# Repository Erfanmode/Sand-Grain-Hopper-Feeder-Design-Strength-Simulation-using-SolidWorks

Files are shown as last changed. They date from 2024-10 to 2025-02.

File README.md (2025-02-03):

# Sand & Grains Hopper Feeder Design & Strength Simulation using SolidWorks - Spring 2022
In this project, we design a sand and grain hopper feeder for the capacity of 30 Tons. Feeder is able to push out the sand and grains
with high moisture. Additionally, it can withstand powerful winds and high magnitude of earthquakes. Huge shout-out to my dear friend and teammate [Reyhane Nikoobayan](https://github.com/ReyhaneNikoobayan) for her contribution to this project.
{31DD2E23-A9A7-48DF-8576-A2769300EA40}
{AE516640-4FAC-4123-9A2C-66D67296858D}
## This Project Contains:
- Dynamic Force and Static Load Analysis
- Strength of Material Estimation
- Design using SolidWorks
- Finite Element Analysis
- Grain Slipping Analysis
- Welded Surface Tension Analysis
- Bolt and Screw Tension Analysis
- Steel Beam Strength Analysis

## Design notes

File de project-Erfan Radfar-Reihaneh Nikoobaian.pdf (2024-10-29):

## به نام خدا

گزارش پروژه پیچ و جوش درس طراحی اجزاء 1

اعضاء:

ریحانه نیکوبیان 99106747 عرفان رادفر 99109603

نام استاد : دکتر محمد دورعلی

خرداد 1401

فهرست

-2 فهرست

-3 صورت مسئله

-4 محاسبات اولیه

-6 به دست آوردن ضخامت ورق ها

-7 وزن اجزاء و نیروهای وارده

-7 جوش نبشی به مخزن بال

-8 جوش لچکی های پایینی

-9سطح مقطع ستون های اصلی

-10محاسبه ابعاد و تعداد پیچ های نبشی به تیر

-11 پیچ نبشی به لچکی های پایین

-12 نصب در زمین

-13 اجزاء به کار رفته

-14 تخمین قیمت

-15 منابع

-16 نقشه ها

صورت مسئله:

سیلوی مصالح دانه بندی شده

در کارخانجات صنایع معدنی موارد زیاد پیش میآید که مصالح ساختمانی مانند شن و ماسه در ابعاد مختلف باید بطور مجزا انبار شوند . این کار بدلیل آن است که بعدا در زمان استفاده مثال برای ساخت بتن یا آسفالت بتوانند با ترکیب های مختلف از این مصالح استفاده کنند . پروژه این دفعه ما در مورد طراحی برای ساخت این سیلو هاست . اگر جمله کلیدی "سیلوی ذخیره مصالح دانه بندی شده" را در مرور گر جستجو کنید و تصاویر را نگاه کنید تعداد زیادی از آنها را مشاهده میکنید . معمول این سیلو ها دارای یک بخش مکعبی در بال و یک بخش هرمی در پایین با یک حفره در پایین ترین قسمت برای تخلیه مواد هستند . حفره پایین با یک دریچه لولیی بسته شده که در موقع تخلیه باز میشود . مواد از بال به داخل آنها ریخته شده و از پایین خارج میشود . زاویه بخش هرمی را طوری می گیرند که ضمن داشتن بیشترین حجم زاویه مناسب برای سر خوردن مصالح و تخلیه را دارا باشد . این سیلو ها معمول با ورق ساخته شده و پایه های آنها از آلت ساختمانی ساخته میشود که با پیچ و مهره بهم متصل میشوند . این سیلو ها میتوانند دارای پایه های بلند باشند که کامیون مستقیما زیر آنها برود و کامیون را با آنها بارگیری کنند . کامیون دنده عقب به زیر آنها میرود و وقتی پر شد از زیر سیلوخارج میشود . 50داشته باشد و بتوانند m به کارخانه ما سفارش 4 عدد از این سیلو ها داده شده که هر یک ظرفیت 3 کامیون را بارگیری کنند . مشتری بدلیل اینکه محل استقرار این سیلو ها را تغییر میدهد عالقمند است که آنها طوری طراحی شوند که بتوان در حالت دمونتاژ شده با حد اقل ارتفاع و ابعاد آنها را روی تریلر بارگیر ی نموده و در محل با یک جرثقیل نه چندان ظرفیت بال این سیلو ها را دوباره مونتاژ کرد . این سیلو ها را طراحی، نقشه مونتاژی و نقشه های قطعات را استخراج نموده و با ذکر مالحظات ساخت مونتاژی، لیست مواد، و برآورد قیمت اجرای پروژه منجمله هزینه های مهندسی به تفکیک در قالب یک گزارش تحویل دهید .

محاسبات اولیه ابعاد:

در طراحی اعضای این سازه ، به علت عبور کامیون و راننده کامیون و کارکنان محیطی که از سیلو استفاده میشود، ضریب اطمینان را 4 میگیریم.

عرض کامیون حدود 2.4 متر است که آینه ها حدود 10 سانت از عرض کامیون بیشتر است و برای راحتی حرکت کامیون عرض مخزن را 3 متر درنظر می گیریم تا کامیون بتواند مانور داشته باشد. برای طراحی با قابلیت محاسبه راحت تر و تقارن و استفاده از ورق 1.5 *6 طول مخزن را نیز 3 متر در نظر می گیریم.ارتفاع کامیون حدود 3 متر است و ممکن است لبه ای برای بارگیری داشته باشیم و همچنین ماسه ها ک په شوند ارتفاع تیرها تا پیش از مخزن خروجی را 3.8 در نظر می گیریم که با محاسبه ارتفاع قیف و دریچه و طول پیچ شده تیر به مخزن تیر باید به ارتفاع باشد

زاویه ریزش ماسه خیس با توجه به اینکه زاویه اصطکاک ماسه و فولد 22 درجه است در نمودار Jenicke (https://powderprocess.net/Silo_discharge.html) و با توجه به زاویه اصطکاک داخلی 45 درجه است زاویه ریزش ماسه خیس 60 درجه به دست می آید.

3-0.4=2.6

2.6*0.5=1.3

h1= 1.3*tan(60)=2.2517

3 =7.769 m ⁰.4∗0.4∗0.346
3

3∗3∗2.596
3

V hopper=

=4.69 m

50−7.769
3∗3

H tank=

همچنین برای دریچه خروجی ارتفاع را 40 سانتی متر تخمین می زنیم و

با توجه به اینکه پین باید وزن ماسه را تحمل کند و ماسه را سیال در نظر می گیریم پس قطر پین را با در نظر گرفتن تحمل تنش برشی به دست می آوریم.

Ƭy
4

=

(2000∗(4.69+2.25+0.4)∗9.8∗0.4^2) 2∗r

2∗π
Fs=4

r=8.9

Ty=Q/2=370/2=185 MPa

اما ما بر اساس دید مهندسی قطر را 4سانتی متر در نظر می گیریم و برای زدن جوش و جلوگیری از تمرکز تنش 1.5 برابر قطر از لبه بالیی فاصله می گذاریم و فاصله مرکز پین تا لبه بالیی 8 سانتی متر می شود و ارتفاع مثلث قِام الزاویه ما 22 سانتی متر و طول قاعده اش 40 سانتی متر است بنابراین
0.48=0.3*0.4*0.4 می | 3m | زاویه دریچه ما به 84.5 میرسد.همچنین حجم مخزن خروجی ما به
رسد.

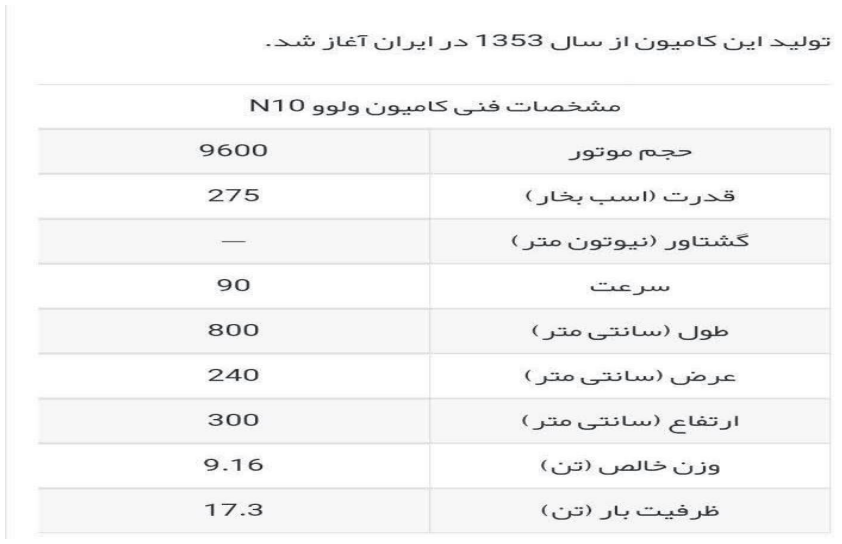
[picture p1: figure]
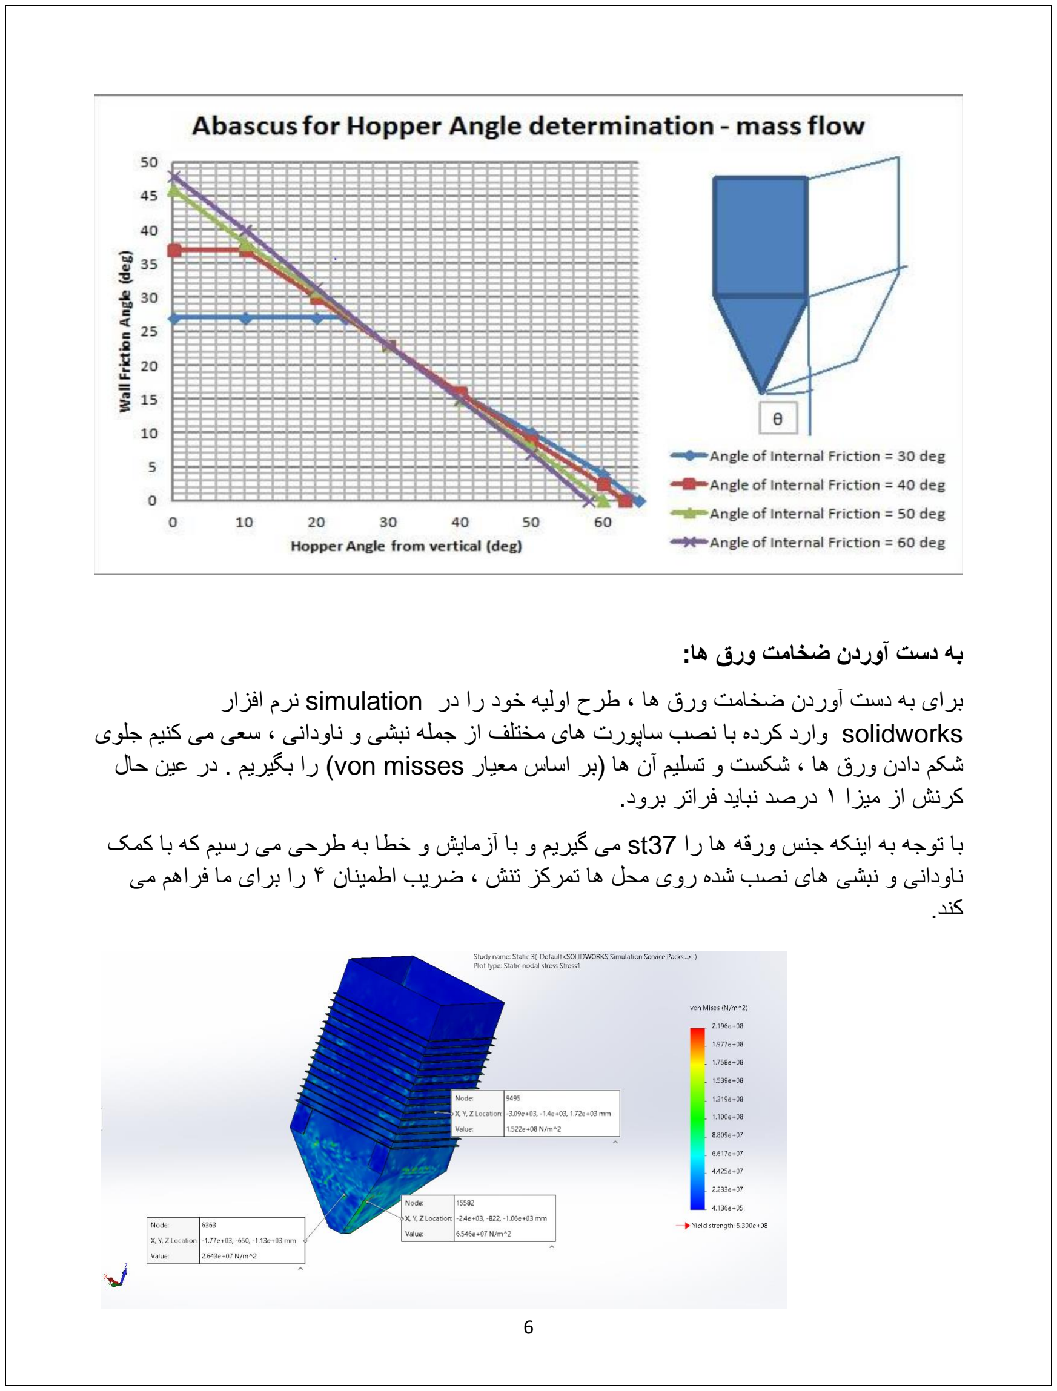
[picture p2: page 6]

به دست آوردن ضخامت ورق ها:

برای به دست آوردن ضخامت ورق ها ، طرح اولیه خود را در simulation نرم افزار solidworks وارد کرده با نصب ساپورت های مختلف از جمله نبشی و ناودانی ، سعی می کنی م جلوی شکم دادن ورق ها ، شکست و تسلیم آن ها ) بر اساس معیار misses von )را بگیریم . در عین حال کرنش از میزا 1 درصد نباید فراتر برود.

با توجه به اینکه جنس ورقه ها را 37st می گیریم و با آزمایش و خطا به طرحی می رسیم که با کمک ناودانی و نبشی ها ی نصب شده روی محل ها تمرکز ت نش ، ضریب اطمینا ن 4 را برای ما فراهم می کند.

در این شبیه سازی محل تکیه گاه، محا نصب ستون ها در نظر گرفته شده تا شرایط سازه اصلی از نظر اعمال نیرو و تنش مهیا باشد.

KN 44.43=9.81 *8030*12*0.01*4.7 وزن مخزن بال )جداره(

m/kg 8030 | 3 | چگالی فولد

KN 13.93=9.81*8030*0.01)*2.6*1.7*(4 وزن قیف )جداره(

(3∗3∗2.6∗sin(60)−0.4

2
∗0.346)
3

*9.81*2000 وزن قیف )ماسه(

KN 830.0=9.81*2000 *4.7 *3*3 وزن مخزن بال )ماسه(

KN 0.942=0.4*0.4*0.3*2000*9.81 وزن دریچه پایین )ماسه(

KN 0.472=8030*9.81*0.01*5*0.3*0.4 وزن دریچه پایین )جداره(

وزنی که لچکیهای پایینی تحمل می کند = وزن جداره قیف + وزن ماسه قیف + وزن ماسه مخزن

13.93+132.2+830+0.942+0.472=977.5 KN

وزنی که نبشی های متصل بهمخزن بالیی تحمل می کنند=وزن جداره قیف و مخزن + وز ن ماسه قیف و مخزن

13.93+132.2+830+44.43+0.942+0.472=1022 KN

برای وزن ناودانی و نبشی و لچک حدود 20 کیلونیوتون به این اعداد اضافه می شود

8 ناودونی مخزن +حدود 2 ناودونی برای قیف +نبشی بین قیف و مخزن و نبشی های مخزن و قیف16+ لچکی

وزن نبشی ها KN 14=9.81*8030*

-6 42*4500*10

وزن ناودانی ها KN 3.3=9.81*34*10

وزن لچکی ها حدود 2 کیلو نیوتون می گیریم و مجموع وزن اتصالت به 20 کیلونیوتون می رسد

جوش نبشی به مخزن باال:

نیرویی که به جوش نبشی متصل کننده ستون ها و بدنه وارد میشود حاصل از نیروی باد ) با استفاد ه از جداول استاند ا (https://eurocodeapplied.com/design/en1991/wind-force-rectangular)رد (https://eurocodeapplied.com/design/en1991/wind-force-rectangular) برای سطح مقطع مستطیلی بدست میآید.( و همین طور نیروی حاصل از اصطکاک

ماسه های داخل مخزن که نسبت کمی از وزن )در حدود 10 درصد ( را دارد. اما با توجه به اینکه سازه ما باید در مواقع زلزله هم با بار پر ، بتواند پایستار باقی بماند می بایست بتواند حداکثر شتاب افقی زلزله (https://en.m.wikipedia.org/wiki/Peak_ground_acceleration) را تحمل کند .

این مقدار برای زلزله هایی با شدت ت خریب 9 )زلزله ای مانند زلزله بم( کمتر از شتاب جاذبه زمین می-باشد. برای همین در محاسبات ، نیرویی افقی برابر وزن مخزن و ماسه به سازه وارد میشود.

در هنگا م زلزله ، جوش نبشی در دو تیر با نیرو ی حداکثر، نیروی 890 کیل ونیوتن را تحمل میکند. از طرفی چون نیروی تیر با فاصله تقریبا نصف عرض نبشی به آن وارد می شود، خمش نیز برای خط جوش بال و پایی ن آن رخ میدهد.)تنش خمش حدود نصف تنش برش می باشد.(

در نتیجه با توجه به معاد له زیر ، حداکثر تنش بر شی در کمترین سطح جوش بدست میآید.

Tmax=

F
0.707.ℎ.l

+

F∗

d
2

∗

d
2
0.707.ℎ.b.

d2
2

= 1.5

F
0.707.ℎ.l

=

94∗ 10⁶

4

Fs=4

∑M=0 47*4.7+1042*2.35=3*F2

Min(0.4Sy;0.3Su)=94

Sy=235 Mpa ; Su=370 Mpa

3∗(44+100+4∗f)∗10³

2∗(0.707∗16∗ℎ)

=

94
4

∗ 10⁶
f=445KN | h=10.9 mm

چون ضخامت 10 میلی متر است جوش 7 میلی متر می زنیم.) از 0.7 ضخامت ورق ، ارتفاع جوش بیشتر نمیشود.(

ضریب اطمینان و طراحی کاهش مییابد اما چون زلزه در مدت کوتاه و احتمال کمی رخ می دهد ، این کاهش ضریب اطمینان قابل قبول است.

جوش لچکی های پایین ی :

لچکی ها می باید نیروی وزن قیف و شنوماسه بالی آن را تحمل کند . پا فرض ارتفاع جوش mm7 به طول جوش زیر میرسیم.

977.5∗10³

0.707∗0.007∗l

=

94∗10⁶

4∗2

L=16.808 m

چون طول جوش خورده لچکی ها از دو طرف cm30 می باشد )15 سانت از سطح لچکی از د و وجه به نبشی و بدنه قیف تماس دارد. ( پس به 14 لچکی از هر طرف نیاز داریم.

هر طرف 14 لچکی 56=16.808/0.3=N

با توجه به ضخامت لچکی ها ) ضخامت هر لچکی 10 میلی متر از ورق مورد استفاده د ر بدنه( نگرانی نسبت به شکست و تسلیم آن ها نداریم.

سطح مقطع ستون های اصلی:

چهار ستون اصلی تحت نیروی عمودی ، در معرض کمانش قرار خواه ند گرفت. با توجه به شکل کمانش آن ها ) یک سر درگیر و یک سر آزاد ( از معادله زیر استفاده میکنیم.

Pcr=

π

2
.E .I
L

2

Le=2L L=3.8+0.4+2.44=6.64m E =206 Gpa

Pcr=445+261=706 KN

Imin=22.6*10⁻⁵ m⁴

2 | اندازه Imin برابر با

cm22600 به دست میآید که همچین تیری در جدول تیرهای استاندارد نداریم.
اما می توانیم تیری با Imax فوق به دست آورده و در راستای عمود محور ممان ضعیف آن ، تیرهای ضربدری را قرار ده یم که باعث میشود طول موثر تیرها در راستای کمانش کاه ش یابد و تیر تقو یت شود.

Iy=22930 cm⁴

Iz=6990 cm⁴

) | جدول | از | انتخابی | )Imin=7890 | HE-A PBI 320

با توجه به مطالب بال تیر 320 PBA A-HE را از جدول انتخاب می کن یم.

جوش تیر به فلنج باالیی:

برای اتصال تیرها به بد نه از پیچ استفاده می کنیم تا قابلیت دمونتاژ شدن داشته باشد. برای اینکه تیره ای به صورت عمودی زیر نبشی مخزن بالیی نصب شوند ) برای کا هش ارتفاع موثر(، بایند فلنجی به سر بالیی آن ج وش دهیم تا و سپس سوراخ پیچ ها را بر روی آن و نبشی ایجاد کنیم.

این جوش باید بتواند نیروی برشی باد و زلزله را تحمل کند.

Tmax=

F
0.707.ℎ.l
N 1089(=نیروی باد(+47(نیروی زلزله)1042=F 94 ∗ 10⁶
4

=

1089 ∗ 10³
4 ∗ 0.707 ∗ ℎ ∗ 1.8

h=9.1 mm

اما ما جوش تیر را 7 میلی متر می زنیم که کمی ضریب اطمینان را تنها در برابر زلزله پایین می اورد که البته به خاطر احتمال کم زلزله و مدت کوتاه آن، این ضریب قا بل قبول است. )3.07=Fs )

محاسبه ابعاد و تعداد پیچ های نبشی به تیر:

اولین گزینه : پیچ 6.8

τ max=√τ
2 +

σ²
4
σ = x ∗ Sp

Sp=0.85 Sy

موقع زلزله

Sp
4

2
>(

X.Sp
2

−

706
N.At

)

2+(Fs.706
N.Ar

)

2

Sp=0.85(600*0.8)=408 MPa

Fs=4 Ar=52.3 mm²

x=0.9 At=58 mm²

ترم اول در محاسبات کوچکتر از صفر می شود پس نیروی عمود بر سطح پیچ ها وارد نمیکند و آن را صفر می گذاریم.

204 > ( ⁴∗272
N∗52.3

تعداد پیچ 101=N)

زلزله نباشد

204>√183.6
2 +

47
N.Ar.10³

تعداد پیچ 10=N

290/25=11

در نتیجه ب ه حدود 100 پیچ برای هر ستون نیاز داریم اما تعداد پیچ ز یاد به قیمت افزایش ابعاد فلنج جوش شده به تیر تم ام میشود پس 60 پیچ قرار می دهیم که ضریب اطمینان را تا 2.4 پایین میآورد.

اما به علت احتمال کم زلزله و نیروی کوتاه مدت آن ، این اندازه قابل قب ول است.

د ر انتها باید دقت شود که در سر تیرها به خاطر اعمال نیرو در سطح کم، احتمال خم شد ن و پیچش نبشی بالیی وجود د ارد، پس در آن نقاط برای هر سطون 5، لچکی در داخل نبشی به دو طرف جوش میدهیم تا مانند خرپ ا عمل کند. لچک ی ها ضخامت 10 و مثلث های قائ م الزا ویه به ابعاد 150* 150 می باشد که 20 میلی متر از راس آن ها بریده شده است. جوش ماهیچه ی آن ها سرتاسری و به ارتفاع 7 میلی متر خواهد بود.

پیچ نبشی به لچکی های پایین

برای اتصال لچکی هایی که قیف پایی ن را نگه داشت ه اند ، از یک فلنج با طول بلند استفاده می شود )1650 میلی متر تا با ستو ن ها تالقی پیدا نکنند (. سپس نبشی مخزن بالیی و فلنج به هم پیچ می-شوند. محاسبه نیروی پیچ آن ها مانند محاسبه نیروی جوش آن هاست، با این تف اوت که به علت وج ود اهرم کوچک لچکی، خمش نیز اتفاق می افتد و تا دو برابر نیرو را با ل می برد.

در عین حال نکته مهم در این قسمت این است که فسردگی فلنج و نبشی نباید صفر شود و همیشه باید نیروی عمود ی اعضای بین پیچ و مهره منفی )فشردگی( بماند.

پس

X∗At∗Sp
FS >

(1−C) ∗ F
N∗4

که c در آن نسبت kb به مجموع kb و km می باشد. با توجه به اینکه برای دو ورق هم ضخامت و با ضخامت نزدیک به قطر پیچ ، c بین 2 و 2.5 می باشد و اینکه F محاسبه شده و At با توجه به پیچ 10 با گر ید 6.8 به دست م ی آید

F=977.5 N

) این نیرو همان نیرو قیف و ماسه بالی آن است (

اندازه N به دست می آید. این اندازه برای هر وجه مخزن است که برابر 44 پیچ می باشد. این پیچ ها در دو ردیف و به تعدا 22 در هر ردیف روی نبشی تعبیه خواهد شد.

نصب در زمین:

با توجه به اینکه وزن مخزن و قیف ر وی همدیگر 6 تن می باشد، نصب آن با جرثقیل های معمول ممکن است.

برای نصب به پایین هر کدام از مخزن هاbolt anchor وصل می شود که با توجه به این که این پیچ در خاک و بتن پایه فرو می رود ، محاسبات آن مرب وط به رشته عمران خواهد بود. در عین حال بهتر است که این مخزن در محل وزش باد شدید و خاک سست نصب نشود.

اجزاء به کار رفته:

ورق ها )همگی از جنس 37st و ضخامت 10 میلی متر(

| تعداد شکل )mm )
1500 *3000 | 12
3000*200 | 4
ارتفاع 1300 | 4 ذوزنقه ای)در نقشه قاعده ها مشخص شده(
ارتفاع 1500 | 4 ذوزنقه ای)در نقشه قاعده ها مشخص شده(
400*400 | 2
دایره | 2 400*400 با یکی از اضالع قسمتی از

پروفیل ها

| | نام قطعه طول ) mm )تعداد
4 | 6800 | HE-A PBA 320
| | ناودانی 200 2750 32
| | نبشی 150 3000 4
4 | 2500 | نبشی 150 )زاویه میان )102.45
| | نبشی 150 3800 4
| | نبشی 150 4500 4

پیج و مهره ها

576 پیچ و مهره 10 میلی متر – گرید 6.8

جوش ها )6013E )

| نوع ضخامت)mm (طول خط جوش(mm (محل جوش
به یکدیگر)افقی ( | مغزی - 12*3000 ورق های مخزن بالیی
| مغزی - 4*0.4 مکعب دریچه
یکدیگر | مغزی - (1607+1793)*4 ورق های قیف ها به
به یکدیگر) عمودی ( | ماهیچه ای 5 4*4700 ورق های مخزن بالیی
| ماهیچه ای 7 3000*8 نبشی به مخزن
| ماهیچه ای 5 4000*32 ناود ان ی ها به مخزن
| ماهیچه ای 7 300*56 لچکی ها به قیف
| ماهیچ ه ای 7 300*20 لچکی بین نبشی

تخمین قیمت:

| جنس قیمت ) هزار تومان(
| نبشی ها) 22 هزارتومان هر 12 متر( 120
| ناودانی)20 هزارتومان هر 12 م تر( 146
| پیچ و مهر ه)250 تومان پیچ و مهره( 144
| تیراهن 320 )هر 12 متر 65 هزار ت ومان( 260
| ورق 10 ، 1500* 6000 = 21.4 هزارتومان 214
6479 | الکترود 6013E ( 2.5 کیلو=167هزارتومان( 97 کیلو برای پروژه
| هزینه برق و تجهیزات جوش 2500
| هزین ه برش ومته 3000
| هزینه حمل و نقل 2800

هزینه کل: 15.6میلیون تومان

منابع:

Calculation method to Design Hoppers and Silos - Hopper and Silo Flow of powder - Flowability issues solving - Discharge throughput (Beverloo equation) (https://powderprocess.net/Silo_discharge.html)

/https://ahanonline.com

https://blog.swantonweld.com/the-various-types-of-structural-steel-shapes (https://blog.swantonweld.com/the-various-types-of-structural-steel-shapes)

https://en.m.wikipedia.org/wiki/Peak_ground_acceleration#:~:text=Pe ak%20Ground%20Acceleration%20(PGA)%20is,site%20during%20a% .20particular%20earthquake (https://en.m.wikipedia.org/wiki/Peak_ground_acceleration)

https://kimyas.ir/%D9%82%DB%8C%D9%85%D8%AA-%D9%BE%DB%8C%DA%86-%D9%88-/%D9%85%D9%87%D8%B1%D9%87 (https://kimyas.ir/%D9%82%DB%8C%D9%85%D8%AA-%D9%BE%DB%8C%DA%86-%D9%88-%D9%85%D9%87%D8%B1%D9%87/)

https://www.geotechdata.info/parameter/angle-of-friction

https://eurocodeapplied.com/design/en1991/wind-force-rectangular#:~:text=The%20basic%20wind%20velocity%20is,provided .%20in%20the%20National%20Annex (https://eurocodeapplied.com/design/en1991/wind-force-rectangular)

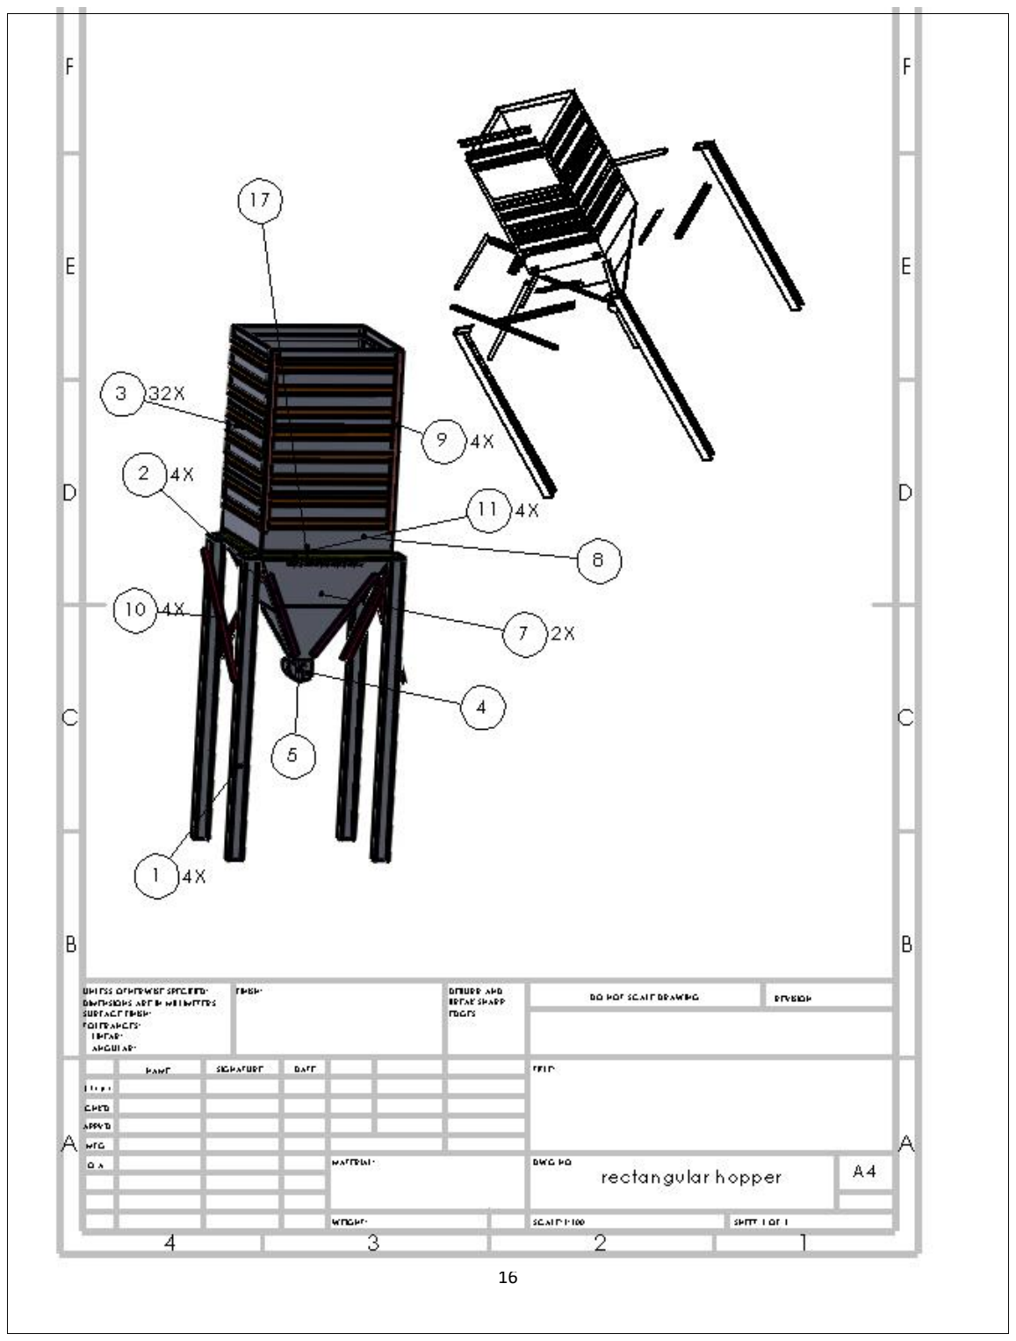
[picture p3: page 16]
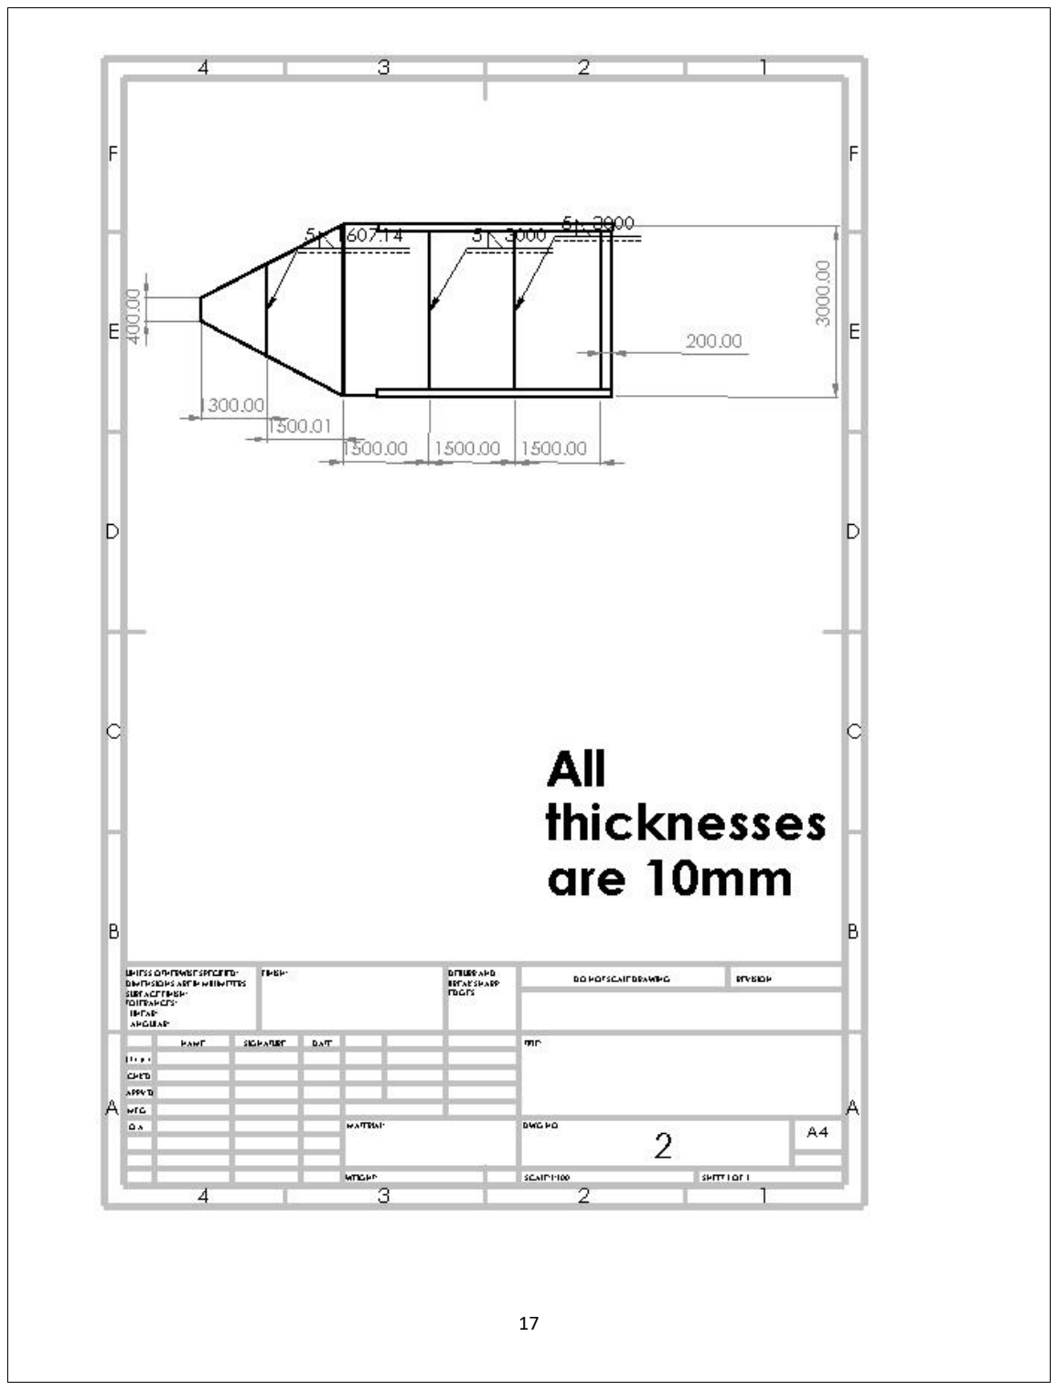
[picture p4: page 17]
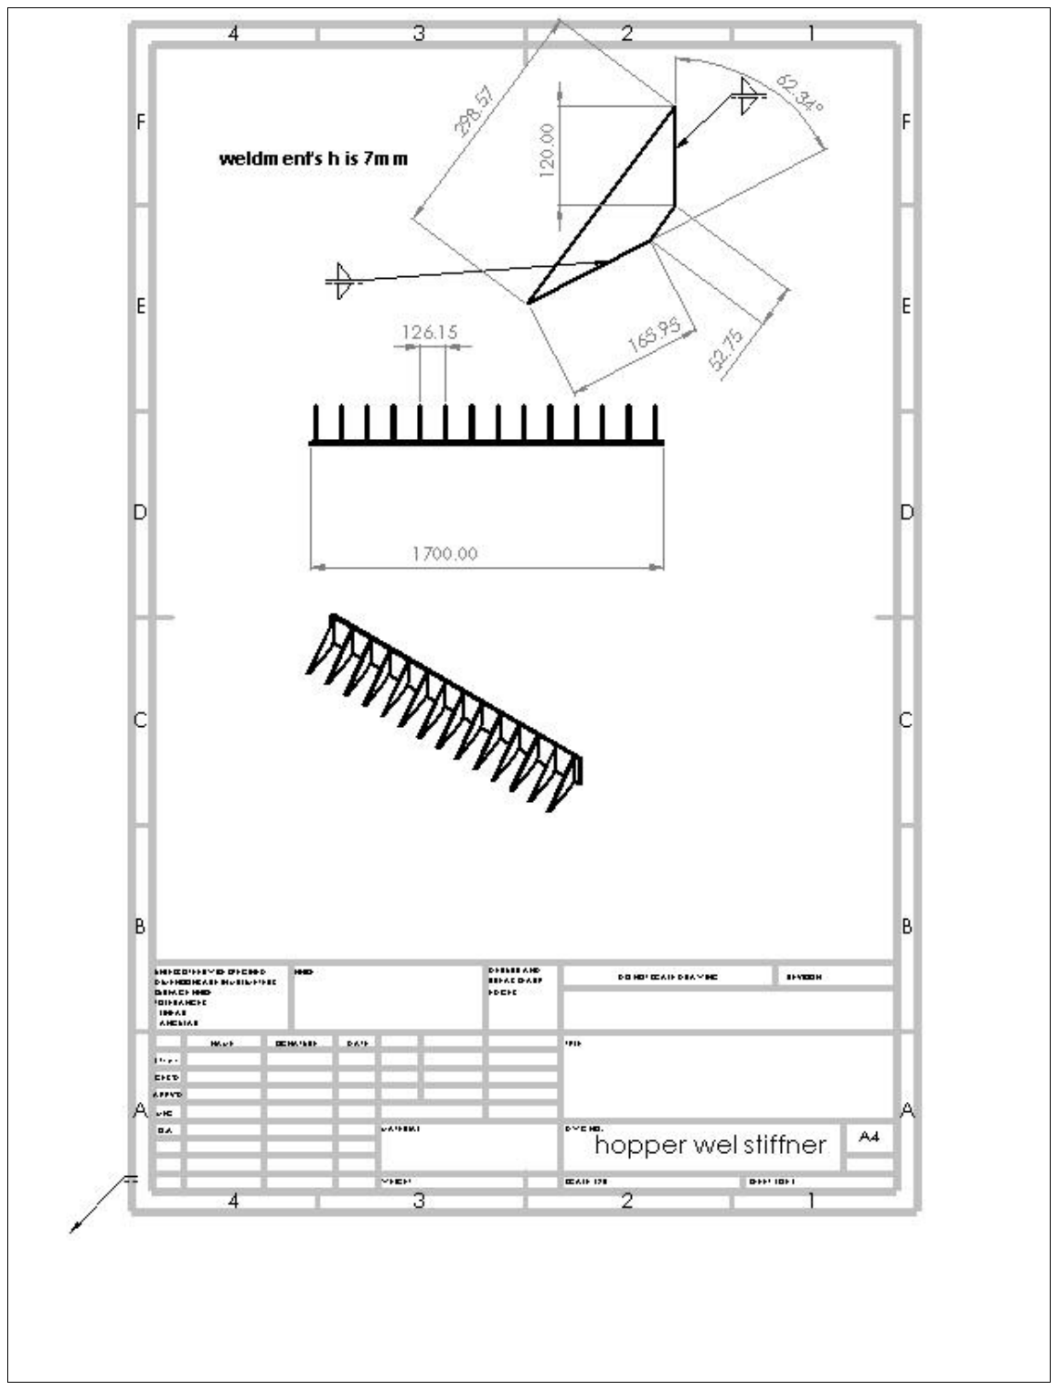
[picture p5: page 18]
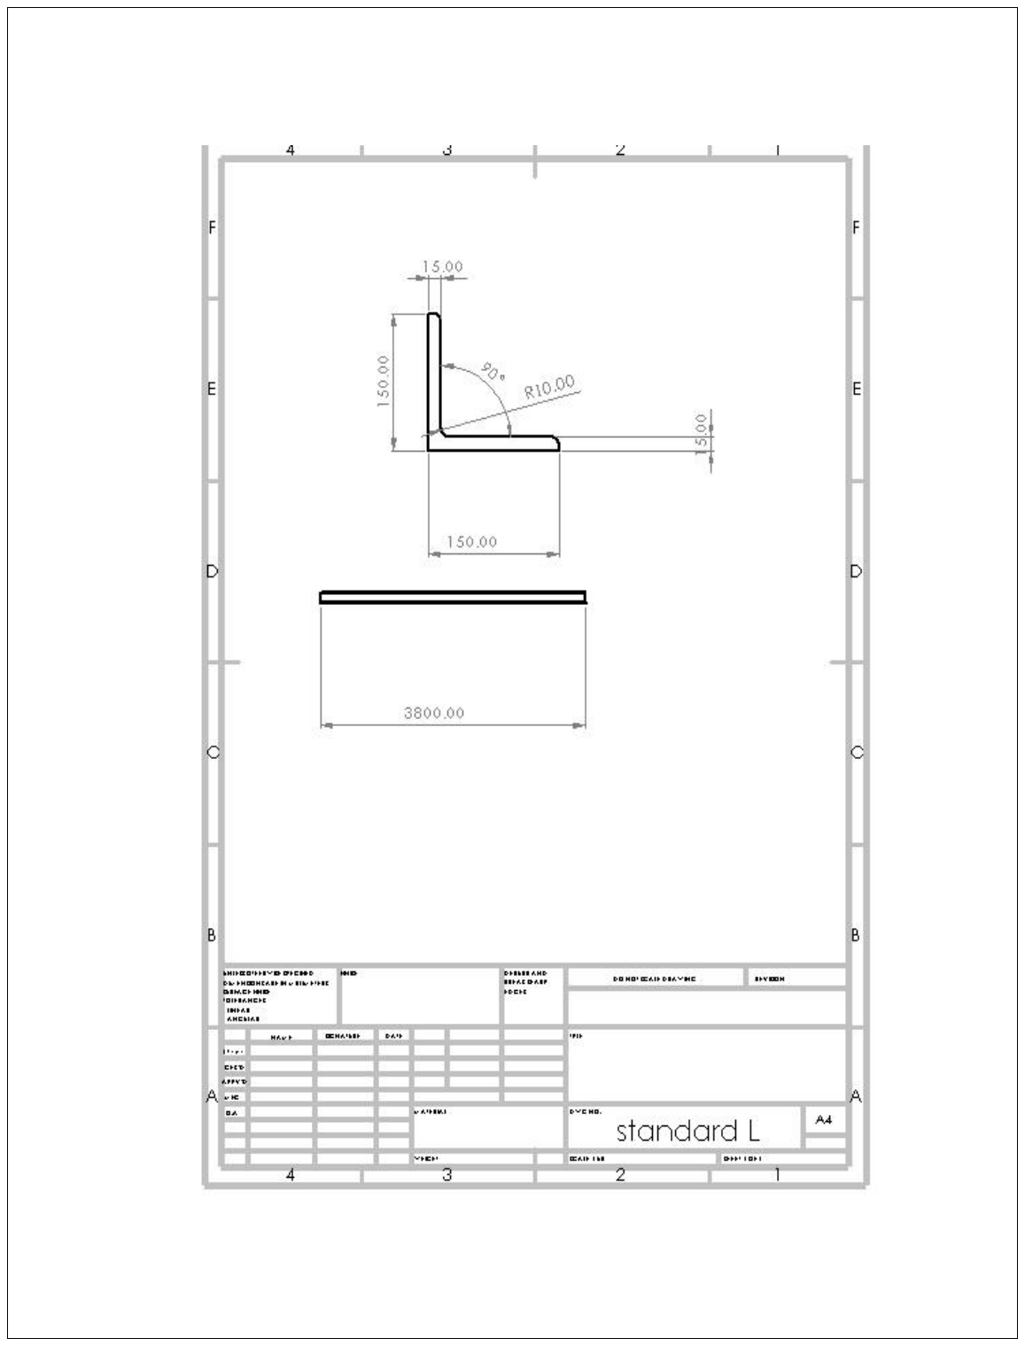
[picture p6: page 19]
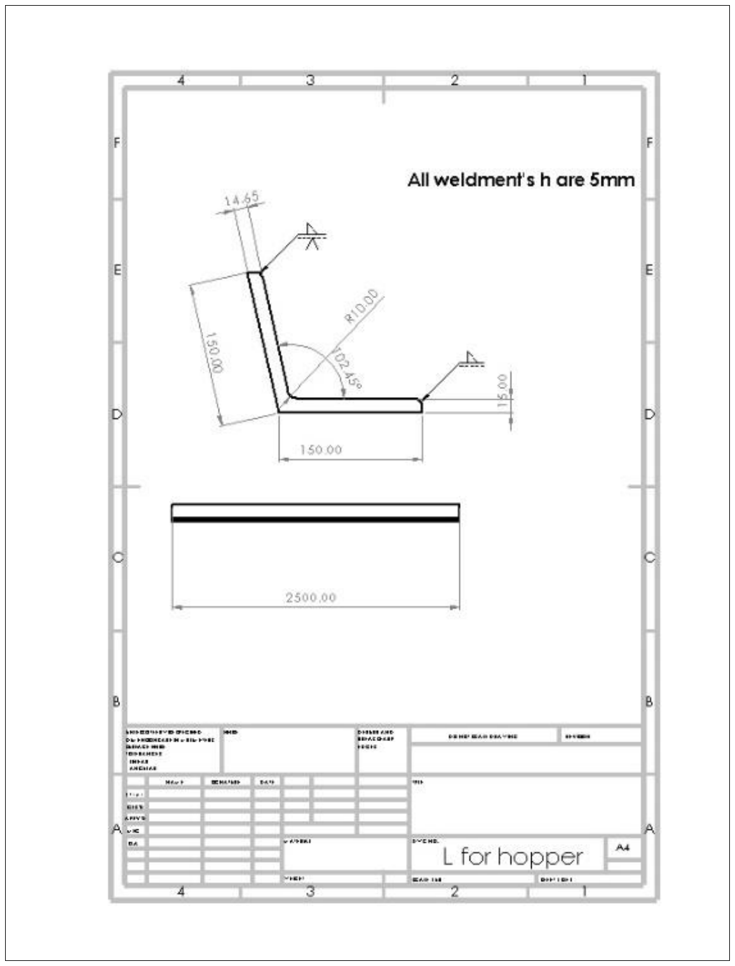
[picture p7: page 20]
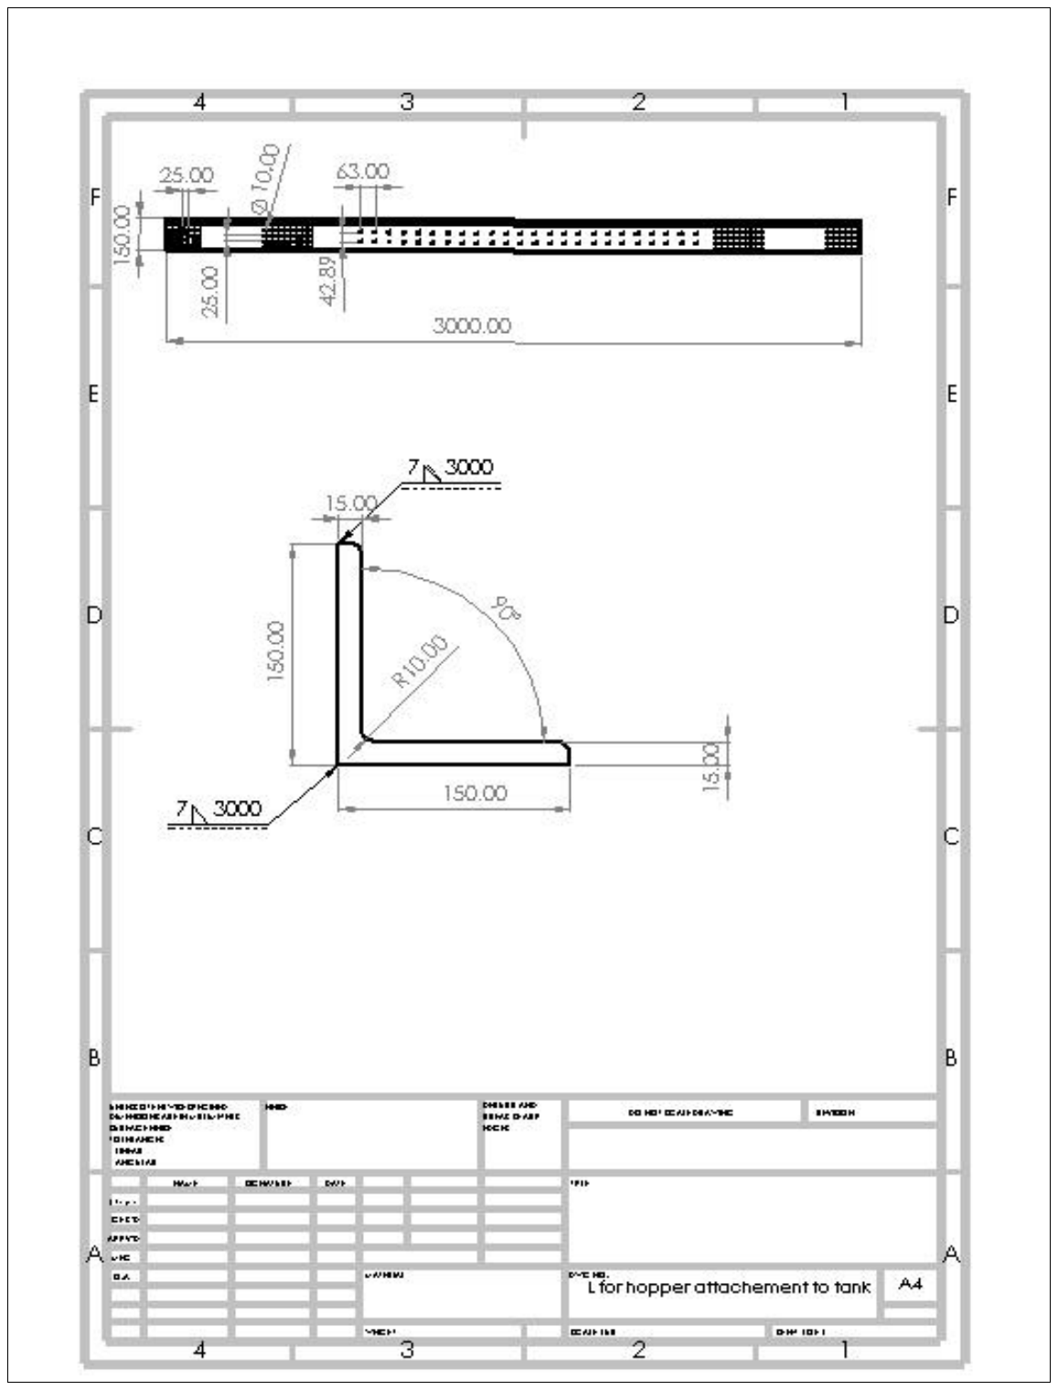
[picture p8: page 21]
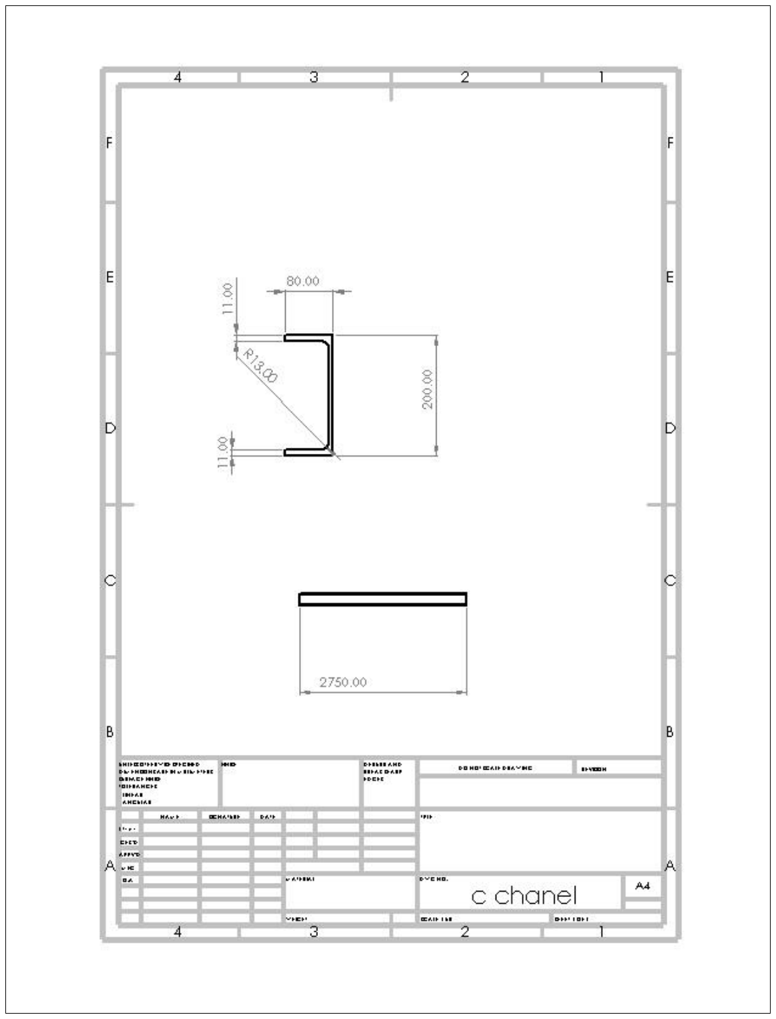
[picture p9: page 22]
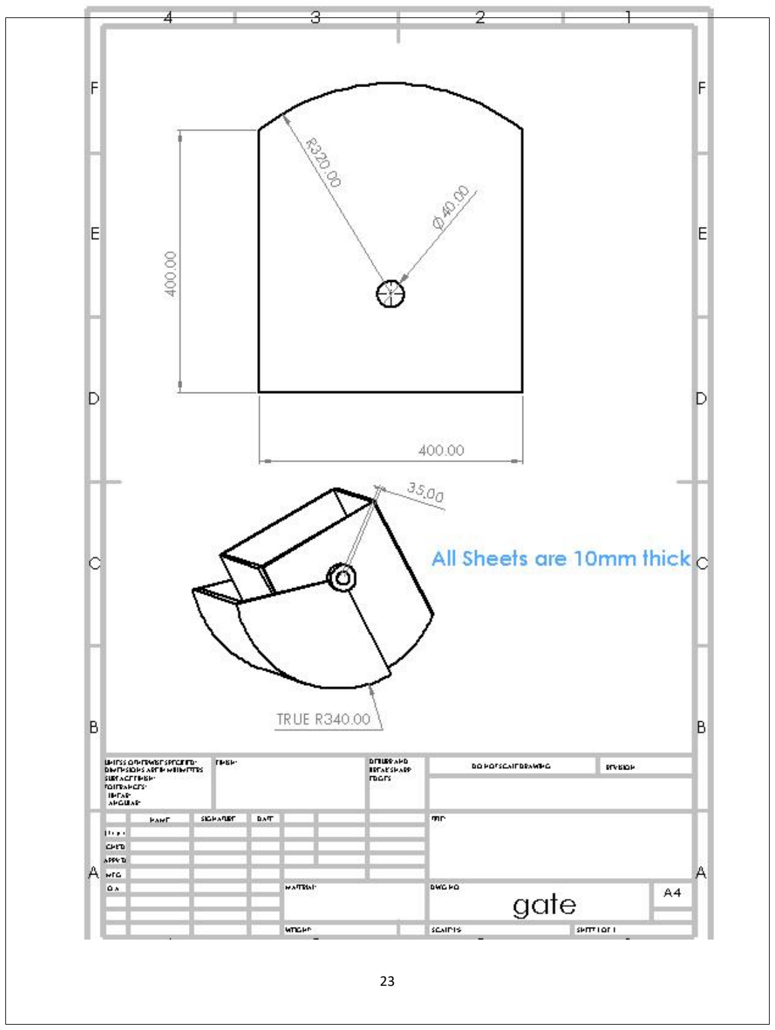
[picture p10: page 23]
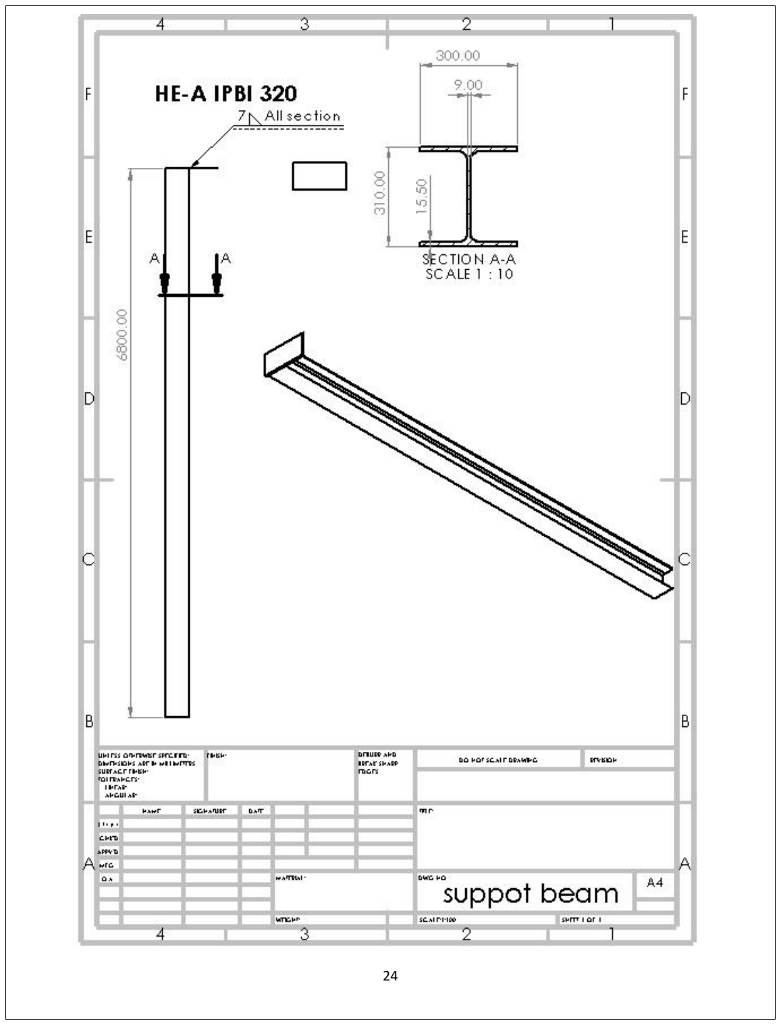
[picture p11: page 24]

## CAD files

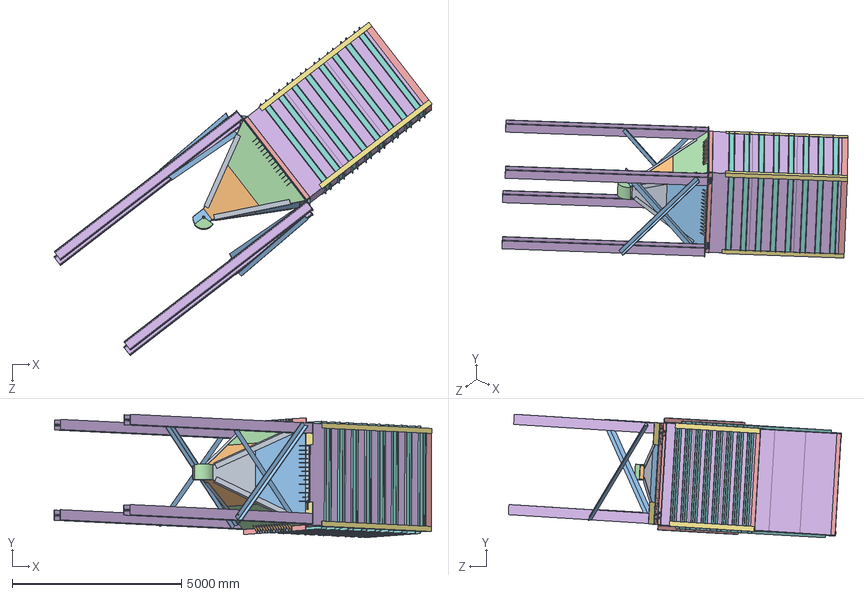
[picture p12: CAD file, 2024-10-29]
Assembly.SLDASM
11162.0 x 3646.3 x 9848.4 mm
1A x 2
1ََB x 2
2A x 2
2B x 2
storage2 x 4
storage1 x 13
L x 4
c chanel x 32
L for hopper x 4
gage1 x 2
gage2 x 2
gage3
L for tir x 4
tir x 4
flange-tir x 4
wel 1 x 20
long flange x 4
wel 2 x 56
L for brace x 4

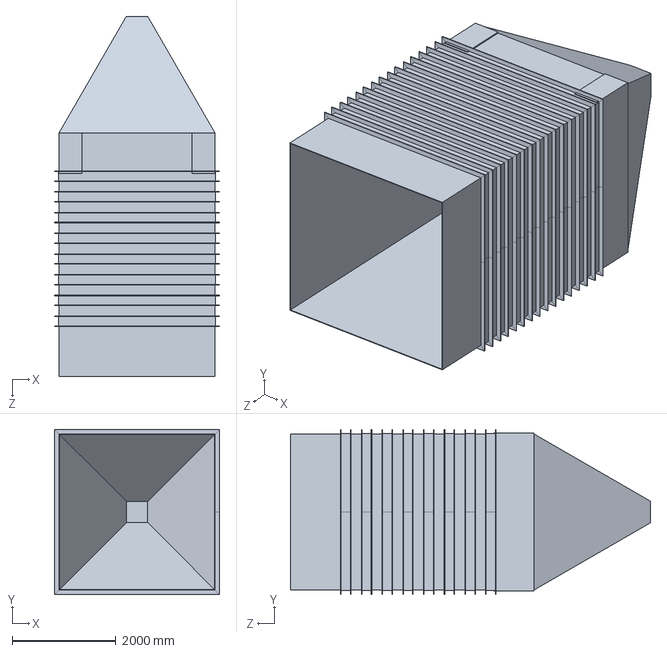
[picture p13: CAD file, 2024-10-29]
Hopper.SLDPRT
3186.7 x 3186.7 x 6961.7 mm

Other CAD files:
1.SLDDRW
2.SLDDRW
3.SLDDRW
4.SLDDRW
5.SLDDRW
6.SLDDRW
c chanel.SLDDRW
gage2.SLDDRW
tir subassem.SLDDRW
